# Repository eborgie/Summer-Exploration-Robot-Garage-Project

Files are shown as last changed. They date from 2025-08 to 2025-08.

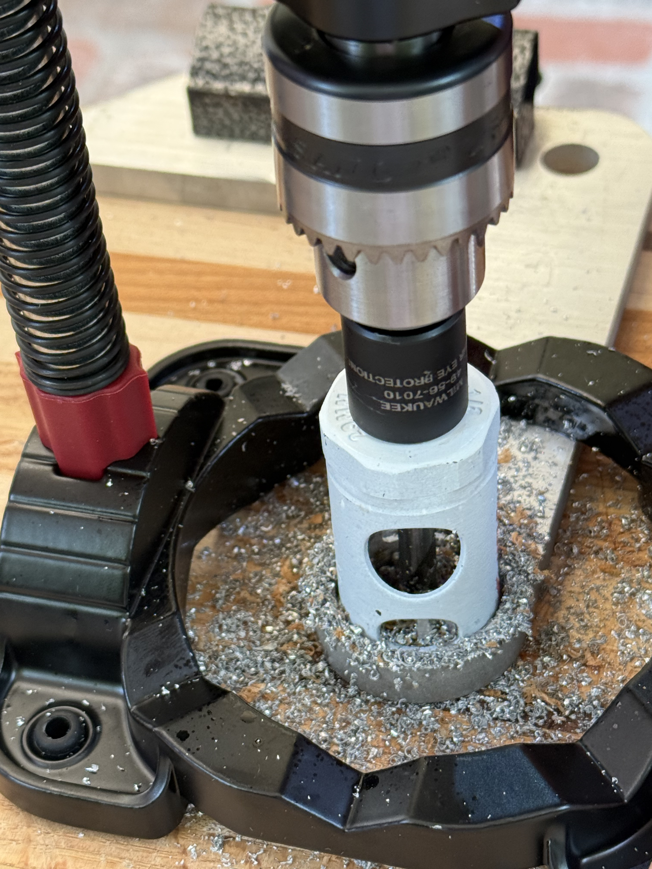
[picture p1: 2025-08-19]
IMG_4325.jpeg

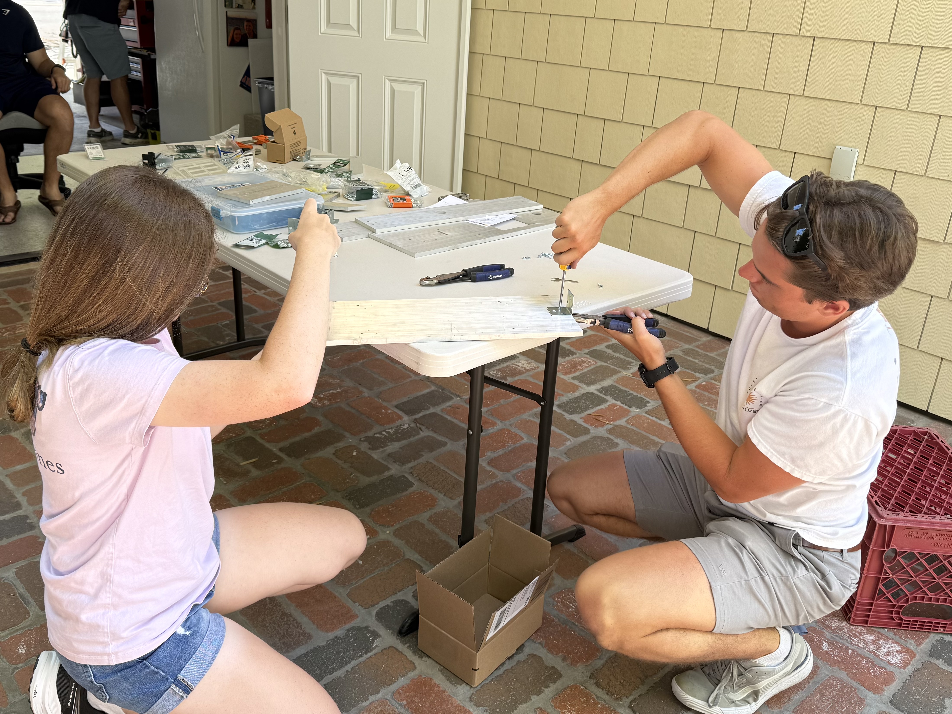
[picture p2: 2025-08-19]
IMG_4257.jpeg

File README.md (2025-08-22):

Iteration 1: Original Aluminum Chassis



Iteration 2: Chassis with Thin Steel sides and Aluminum top and bottom





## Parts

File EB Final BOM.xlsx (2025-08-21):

Final Design BOM | Part Name | # Of Parts | Unit Price | Total Cost | Preliminary sourcing link(s) | Categorical Statistics | Categorical Values
Chassis |  |  |  |  |  | # Of Unique Chassis Parts | 1
Aluminum Sheet |  | 1 | $169.80 | $169.80 | https://www.mcmaster.com/9246k475/ | Total # Of Chassis Parts | 1
 |  |  |  | $0.00 |  | Average Unit Price | $169.80
 |  |  |  | $0.00 |  | Total Chassis Cost | $169.80
 |  |  |  | $0.00 |  | Percent of Current Budget | 15.93%
 |  |  |  | $0.00 |  | Percent of Total Budget | 16.98%
SELECT AND INSERT NEW ROW ABOVE HERE |  |  |  | $0.00
Suspension & Steering |  |  |  |  |  | # Of Unique S&S Parts | 7
Aluminum Sheet |  | 1 | $169.80 | $169.80 | https://www.mcmaster.com/9246k475/ | Total # Of S&S Parts | 13
Wheel tires (4 pack) |  | 2 | $14.97 | $29.94 | https://www.amazon.com/4-Pack-HobbyPark-2-99-inch-Rubber/dp/B071ZX9JB7 | Average Unit Price | $37.37
Series 20 Motor | 195:1 Metal Gearmotor | 6 | $33.07 | $198.42 | https://www.pololu.com/product/3481 | Total S&S Cost | $441.88
dowel pins-short |  | 1 | $9.11 | $9.11 | https://www.mcmaster.com/98381A910/ | Percent of Current Budget | 41.45%
joint bearings |  | 1 | $9.99 | $9.99 | https://www.amazon.com/dp/B0CXXBHWCX?sp_csd=d2lkZ2V0TmFtZT1zcF9kZXRhaWw | Percent of Total Budget | 44.19%
Bolts |  | 1 | $11.15 | $11.15 | https://www.mcmaster.com/91310a124/
female ends |  | 1 | $13.47 | $13.47 | https://www.amazon.com/dp/B0CV43VQHN?aref=0ED2V8mSYO
 |  |  |  | $0.00
 |  |  |  | $0.00
 |  |  |  | $0.00
 |  |  |  | $0.00
SELECT AND INSERT NEW ROW ABOVE HERE |  |  |  | $0.00
Sample Arm |  |  |  |  |  | # Of Unique SA Parts | 4
6mm shaft 2ft [609mm] CHECK ELSEWHERE 6MM | Linear shaft Diameter: 4mm Length: 600mm | 1 | $22.67 | $22.67 | https://shop.pbclinear.com/collections/linear-shafting-and-rails/products/nim04-0600-sl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 | Total # Of SA Parts | 5
Series 20 Motor Extended Shaft | 195:1 Metal Gearmotor with Extended Motor Shaft | 2 | $36.35 | $72.70 | https://www.pololu.com/product/3493 | Average Unit Price | $20.61
Micro Servo | HS-55 Servo-Clockwise (Servo) | 1 | $13.49 | $13.49 | https://www.servocity.com/hs-55-servo/ | Total SA Cost | $118.81
Motor Encoder | Magnetic Encoder Pair Kit for 20D [2 included] | 1 | $9.95 | $9.95 | https://www.pololu.com/product/3499 | Percent of Current Budget | 11.14%
 |  |  |  | $0.00 |  | Percent of Total Budget | 11.88%
SELECT AND INSERT NEW ROW ABOVE HERE |  |  |  | $0.00
Electronics |  |  |  |  |  | # Of Unique Electronics Parts | 9
L298N Motor Controller | 4 Pack L298N Motor Drive Controller Board | 1 | $9.99 | $9.99 | https://www.amazon.com/Controller-H-Bridge-Stepper-Control-Mega2560/dp/B07WS89781?gQT=1 | Total # Of Electronics Parts | 10
Stepper Motor - NEMA 17 |  | 1 | $12.99 | $12.99 | https://www.amazon.com/Stepper-Motor-Bipolar-64oz-Printer/dp/B00PNEQI7W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 | Average Unit Price | $24.88
A4988 Stepper Driver |  | 1 | $10.19 | $10.19 | https://www.amazon.com/HiLetgo-Stepstick-Stepper-Printer-Compatible/dp/B07BND65C8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 | Total Electronics Cost | $250.85
Arduino MEGA |  | 1 | $50.94 | $50.94 | https://www.amazon.com/ARDUINO-MEGA-2560-REV3-A000067/dp/B0046AMGW0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 | Percent of Current Budget | 23.53%
DC-DC Buck Conveter |  | 1 | $11.99 | $11.99 | https://www.amazon.com/XLX-Adjustable-Step-Down-1-25-36V-XL4016E1-Regulating/dp/B07Z8Q6NYX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 | Percent of Total Budget | 25.09%
3S LiPo Battery |  | 1 | $26.99 | $26.99 | https://www.amazon.com/1800mAh-M4-FPV250-Shredder-Nighthawk-Airplane/dp/B013I9SAHO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
XT60 Connector |  | 1 | $13.99 | $13.99 | https://www.amazon.com/dp/B07CN3RZRF?sp_csd=d2lkZ2V0TmFtZT1zcF9kZXRhaWxfdGhlbWF0aWM
Servos | 25 KG Digital Servo [2 included] | 2 | $26.89 | $53.78 | https://www.amazon.com/DS3225-Waterproof-Digital-Aluminium-Steering/dp/B08RJGVH7D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
Rc set |  | 1 | $59.99 | $59.99 | https://www.gobilda.com/element-6-radio-control-system-mode-2/
 |  |  |  | $0.00
 |  |  |  | $0.00
 |  |  |  | $0.00
SELECT AND INSERT NEW ROW ABOVE HERE |  |  |  | $0.00
Interfacing (collars, hubs, couplers, fasteners) |  |  |  |  |  | # Of Unique Interfacing Parts | 5
Shaft Collar | Universal Mounting Hub for 4mm Shaft, M3 Holes [2 included] | 1 | $10.95 | $10.95 | https://www.pololu.com/product/1997 | Total # Of Interfacing Parts | 18
Lazy Susan Bearing | 2" Lazy Susan Turntable | 1 | $3.99 | $3.99 | https://www.amazon.com/Turntable-Bearing-Rotating-Cabinet-Profile/dp/B0BHQQMG71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 | Average Unit Price | $9.19
Dowel Pins | Dowel Pins 1" Diameter, 1.5" Length | 1 | $17.14 | $17.14 | https://www.mcmaster.com/products/dowel-pins/length~10/length~1-1-4/ | Total Interfacing Cost | $84.80
Retaining Rings | Self-Locking External Retaining Rings [50ct] | 1 | $10.86 | $10.86 | https://www.mcmaster.com/90341A103/ | Percent of Total Budget | 8.48%
L Brackets |  | 14 | $2.99 | $41.86 | https://www.mcmaster.com/17715a43/
 |  |  |  | $0.00
SELECT AND INSERT NEW ROW ABOVE HERE |  |  |  | $0.00
Total Budget: | $1000.00
 | Unique Items | Total Part Count | Remaining Budget | Total Cost | Percent of Personal Budget Used:
TOTALS | 11 | 47 | -$66.14 | $1066.14 | 106.61%

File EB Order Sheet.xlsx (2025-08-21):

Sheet: Sheet1
Ordered? | Place |  | Items | Number | Cost | Shipping | Individual Total | Total | Recieved
TRUE | McMaster Carr | Dowel Pins | https://www.mcmaster.com/98381A910/ | 1 | $9.11 | $27.84 | $9.11 | $440.42 | TRUE
TRUE |  | Bolts | https://www.mcmaster.com/91310a124/ | 1 | $11.15 |  | $11.15 |  | TRUE
TRUE |  | Retaining Clips | https://www.mcmaster.com/90341A103/ | 1 | $10.86 |  | $10.86 |  | TRUE
TRUE |  | Brackets | https://www.mcmaster.com/17715a43/ | 14 | $2.99 |  | $41.86 |  | TRUE
TRUE |  | Aluminum | https://www.mcmaster.com/9246k475/ | 2 | $169.80 |  | $339.60 |  | TRUE
TRUE | Amazon | Wheels | https://www.amazon.com/4-Pack-HobbyPark-2-99-inch-Rubber/dp/B071ZX9JB7 | 2 | $14.97 | $0.00 | $29.94 | $248.25 | TRUE
TRUE |  | Bearing | https://www.amazon.com/dp/B0CXXBHWCX?sp_csd=d2lkZ2V0TmFtZT1zcF9kZXRhaWw | 1 | $9.99 |  | $9.99 |  | TRUE
TRUE |  | Rod ends | https://www.amazon.com/dp/B0CV43VQHN?aref=0ED2V8mSYO | 1 | $13.47 |  | $13.47 |  | TRUE
TRUE |  | Motor Drivers | https://www.amazon.com/Controller-H-Bridge-Stepper-Control-Mega2560/dp/B07WS89781?gQT=1 | 1 | $9.99 |  | $9.99 |  | TRUE
TRUE |  | Stepper | https://www.amazon.com/Stepper-Motor-Bipolar-64oz-Printer/dp/B00PNEQI7W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 | 1 | $12.99 |  | $12.99 |  | TRUE
TRUE |  | Stepper Driver | https://www.amazon.com/HiLetgo-Stepstick-Stepper-Printer-Compatible/dp/B07BND65C8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 | 1 | $10.19 |  | $10.19 |  | TRUE
TRUE |  | Arduino | https://www.amazon.com/ARDUINO-MEGA-2560-REV3-A000067/dp/B0046AMGW0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 | 1 | $50.94 |  | $50.94 |  | TRUE
TRUE |  | DCDC buck | https://www.amazon.com/XLX-Adjustable-Step-Down-1-25-36V-XL4016E1-Regulating/dp/B07Z8Q6NYX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 | 1 | $11.99 |  | $11.99 |  | TRUE
TRUE |  | Battery | https://www.amazon.com/1800mAh-M4-FPV250-Shredder-Nighthawk-Airplane/dp/B013I9SAHO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 | 1 | $26.99 |  | $26.99 |  | TRUE
TRUE |  | Nylon wires | https://www.amazon.com/dp/B07CN3RZRF?sp_csd=d2lkZ2V0TmFtZT1zcF9kZXRhaWxfdGhlbWF0aWM | 1 | $13.99 |  | $13.99 |  | TRUE
TRUE |  | servos | https://www.amazon.com/DS3225-Waterproof-Digital-Aluminium-Steering/dp/B08RJGVH7D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 | 2 | $26.89 |  | $53.78 |  | TRUE
TRUE |  | Lazy susan | https://www.amazon.com/Turntable-Bearing-Rotating-Cabinet-Profile/dp/B0BHQQMG71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 | 1 | $3.99 |  | $3.99 |  | TRUE
TRUE | Pololu | Motors | https://www.pololu.com/product/3481 | 6 | $33.07 | $9.17 | $198.42 | $306.59 | TRUE
TRUE |  | Motors with rod | https://www.pololu.com/product/3493 | 2 | $36.35 |  | $72.70 |  | TRUE
TRUE |  | Encoder | https://www.pololu.com/product/3499 | 1 | $9.95 |  | $9.95 |  | TRUE
TRUE |  | Universal adapter | https://www.pololu.com/product/1997 | 1 | $10.95 | $5.40 | $10.95 |  | TRUE
TRUE | Servo City/Gobuilda | Mini servo | https://www.servocity.com/hs-55-servo/ | 1 | $13.45 | $5.12 | $13.45 | $73.40 | TRUE
TRUE |  | Radio controller | https://www.gobilda.com/element-6-radio-control-system-mode-2/ | 1 | $59.95 | $11.99 | $59.95 |  | TRUE
 |  |  |  | 45 |  |  | Total | $1068.66 |  | $534.33 | $581.71
 |  |  |  |  |  |  |  |  |  | $47.38
ROUND 2:
FALSE | Amazon | Dshaft | https://www.amazon.com/Favordrory-Stainless-Straight-Helicopter-Airplane/dp/B08L7X3D13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 | 1 | $7.99 |  | $7.99 |  | FALSE
TRUE | Amazon | Wire | https://www.amazon.com/Silicone-Electrical-electronics-stranded-Flexible/dp/B07TGJGJGD?s=industrial | 1 | $14.58 | $0.00 | $14.58 | $22.57 | TRUE
TRUE | Pololu | Motor | https://www.pololu.com/product/3481 | 1 | $33.07 | $8.66 | $33.07 | $41.73 | TRUE
TRUE | Mcmaster Carr |  | https://www.mcmaster.com/98381A716/ | 1 | $17.14 | $10.20 | $17.14 |  | TRUE
TRUE | mcmaster carr |  | https://www.mcmaster.com/91595A154/ | 4 | $12.48 |  | $3.12 | $30.46 | TRUE
FALSE | servo city | servo | https://www.servocity.com/hs-65hb-servo/ | 1 | $25.49 |  | 25.49 |  | FALSE
FALSE |  |  |  | 9 |  |  | Total | $94.76
FALSE
FALSE
FALSE
FALSE
FALSE
FALSE
FALSE
FALSE
FALSE
FALSE
FALSE
FALSE
FALSE
FALSE
FALSE
FALSE
FALSE
FALSE
FALSE
FALSE
FALSE
FALSE
FALSE
FALSE
FALSE
FALSE
FALSE
FALSE
FALSE
FALSE
FALSE
FALSE
FALSE
FALSE
FALSE
FALSE
FALSE
FALSE
FALSE
FALSE
FALSE
FALSE
FALSE
FALSE
FALSE
FALSE
FALSE
FALSE
FALSE
FALSE
FALSE
FALSE
FALSE
FALSE
FALSE
FALSE
FALSE
FALSE
FALSE
FALSE
FALSE
FALSE
FALSE
FALSE
FALSE
FALSE
FALSE
FALSE
FALSE
FALSE
FALSE
FALSE
FALSE
FALSE
FALSE
FALSE
FALSE
FALSE
FALSE
FALSE
FALSE
FALSE
FALSE
FALSE
FALSE
FALSE
FALSE
FALSE
FALSE
FALSE
FALSE
FALSE
FALSE
FALSE
FALSE
FALSE
FALSE
FALSE
FALSE
FALSE
FALSE
FALSE
FALSE
FALSE
FALSE
FALSE
FALSE
FALSE
FALSE
FALSE
FALSE
FALSE
FALSE
FALSE
FALSE
FALSE
FALSE
FALSE
FALSE
FALSE
FALSE
FALSE
FALSE
FALSE
FALSE
FALSE
FALSE
FALSE
FALSE
FALSE
FALSE
FALSE
FALSE
FALSE
FALSE
FALSE
FALSE
FALSE
FALSE
FALSE
FALSE
FALSE
FALSE
FALSE
FALSE
FALSE
FALSE
FALSE
FALSE
FALSE
FALSE
FALSE
FALSE
FALSE
FALSE
FALSE
FALSE
FALSE
FALSE
FALSE
FALSE
FALSE
FALSE
FALSE
FALSE
FALSE
FALSE
FALSE
FALSE
FALSE
FALSE
FALSE
FALSE
FALSE
FALSE
FALSE
FALSE
FALSE
FALSE
FALSE
FALSE
FALSE
FALSE
FALSE
FALSE
FALSE
FALSE
FALSE
FALSE
FALSE
FALSE
FALSE
FALSE
FALSE
FALSE
FALSE
FALSE
FALSE
FALSE
FALSE
FALSE
FALSE
FALSE
FALSE
FALSE
FALSE
FALSE
FALSE
FALSE
FALSE
FALSE
FALSE
FALSE
FALSE
FALSE
FALSE
FALSE
FALSE
FALSE
FALSE
FALSE
FALSE
FALSE
FALSE
FALSE
FALSE
FALSE
FALSE
FALSE
FALSE
FALSE
FALSE
FALSE
FALSE
FALSE
FALSE
FALSE
FALSE
FALSE
FALSE
FALSE
FALSE
FALSE
FALSE
FALSE
FALSE
FALSE
FALSE
FALSE
FALSE
FALSE
FALSE
FALSE
FALSE
FALSE
FALSE
FALSE
FALSE
FALSE
FALSE
FALSE
FALSE
FALSE
FALSE
FALSE
FALSE
FALSE
FALSE
FALSE
FALSE
FALSE
FALSE
FALSE
FALSE
FALSE
FALSE
FALSE
FALSE
FALSE
FALSE
FALSE
FALSE
FALSE
FALSE
FALSE
FALSE
FALSE
FALSE
FALSE
FALSE
FALSE
FALSE
FALSE
FALSE
FALSE
FALSE
FALSE
FALSE
FALSE
FALSE
FALSE
FALSE
FALSE
FALSE
FALSE
FALSE
FALSE
FALSE
FALSE
FALSE
FALSE
FALSE
FALSE
FALSE
FALSE
FALSE
FALSE
FALSE
FALSE
FALSE
FALSE
FALSE
FALSE
FALSE
FALSE
FALSE
FALSE
FALSE
FALSE
FALSE
FALSE
FALSE
FALSE
FALSE
FALSE
FALSE
FALSE
FALSE
FALSE
FALSE
FALSE
FALSE
FALSE
FALSE
FALSE
FALSE
FALSE
FALSE
FALSE
FALSE
FALSE
FALSE
FALSE
FALSE
FALSE
FALSE
FALSE
FALSE
FALSE
FALSE
FALSE
FALSE
FALSE
FALSE
FALSE
FALSE
FALSE
FALSE
FALSE
FALSE
FALSE
FALSE
FALSE
FALSE
FALSE
FALSE
FALSE
FALSE
FALSE
FALSE
FALSE
FALSE
FALSE
FALSE
FALSE
FALSE
FALSE
FALSE
FALSE
FALSE
FALSE
FALSE
FALSE
FALSE
FALSE
FALSE
FALSE
FALSE
FALSE
FALSE
FALSE
FALSE
FALSE
FALSE
FALSE
FALSE
FALSE
FALSE
FALSE
FALSE
FALSE
FALSE
FALSE
FALSE
FALSE
FALSE
FALSE
FALSE
FALSE
FALSE
FALSE
FALSE
FALSE
FALSE
FALSE
FALSE
FALSE
FALSE
FALSE
FALSE
FALSE
FALSE
FALSE
FALSE
FALSE
FALSE
FALSE
FALSE
FALSE
FALSE
FALSE
FALSE
FALSE
FALSE
FALSE
FALSE
FALSE
FALSE
FALSE
FALSE
FALSE
FALSE
FALSE
FALSE
FALSE
FALSE
FALSE
FALSE
FALSE
FALSE
FALSE
FALSE
FALSE
FALSE
FALSE
FALSE
FALSE
FALSE
FALSE
FALSE
FALSE
FALSE
FALSE
FALSE
FALSE
FALSE
FALSE
FALSE
FALSE
FALSE
FALSE
FALSE
FALSE
FALSE
FALSE
FALSE
FALSE
FALSE
FALSE
FALSE
FALSE
FALSE
FALSE
FALSE
FALSE
FALSE
FALSE
FALSE
FALSE
FALSE
FALSE
FALSE
FALSE
FALSE
FALSE
FALSE
FALSE
FALSE
FALSE
FALSE
FALSE
FALSE
FALSE
FALSE
FALSE
FALSE
FALSE
FALSE
FALSE
FALSE
FALSE
FALSE
FALSE
FALSE
FALSE
FALSE
FALSE
FALSE
FALSE
FALSE
FALSE
FALSE
FALSE
FALSE
FALSE
FALSE
FALSE
FALSE
FALSE
FALSE
FALSE
FALSE
FALSE
FALSE
FALSE
FALSE
FALSE
FALSE
FALSE
FALSE
FALSE
FALSE
FALSE
FALSE
FALSE
FALSE
FALSE
FALSE
FALSE
FALSE
FALSE
FALSE
FALSE
FALSE
FALSE
FALSE
FALSE
FALSE
FALSE
FALSE
FALSE
FALSE
FALSE
FALSE
FALSE
FALSE
FALSE
FALSE
FALSE
FALSE
FALSE
FALSE
FALSE
FALSE
FALSE
FALSE
FALSE
FALSE
FALSE
FALSE
FALSE
FALSE
FALSE
FALSE
FALSE
FALSE
FALSE
FALSE
FALSE
FALSE
FALSE
FALSE
FALSE
FALSE
FALSE
FALSE
FALSE
FALSE
FALSE
FALSE
FALSE
FALSE
FALSE
FALSE
FALSE
FALSE
FALSE
FALSE
FALSE
FALSE
FALSE
FALSE
FALSE
FALSE
FALSE
FALSE
FALSE
FALSE
FALSE
FALSE
FALSE
FALSE
FALSE
FALSE
FALSE
FALSE
FALSE
FALSE
FALSE
FALSE
FALSE
FALSE
FALSE
FALSE
FALSE
FALSE
FALSE
FALSE
FALSE
FALSE
FALSE
FALSE
FALSE
FALSE
FALSE
FALSE
FALSE
FALSE
FALSE
FALSE
FALSE
FALSE
FALSE
FALSE
FALSE
FALSE
FALSE
FALSE
FALSE
FALSE
FALSE
FALSE
FALSE
FALSE
FALSE
FALSE
FALSE
FALSE
FALSE
FALSE
FALSE
FALSE
FALSE
FALSE
FALSE
FALSE
FALSE
FALSE
FALSE
FALSE
FALSE
FALSE
FALSE
FALSE
FALSE
FALSE
FALSE
FALSE
FALSE
FALSE
FALSE
FALSE
FALSE
FALSE
FALSE
FALSE
FALSE
FALSE
FALSE
FALSE
FALSE
FALSE
FALSE
FALSE
FALSE
FALSE
FALSE
FALSE
FALSE
FALSE
FALSE
FALSE
FALSE
FALSE
FALSE
FALSE
FALSE
FALSE
FALSE
FALSE
FALSE
FALSE
FALSE
FALSE
FALSE
FALSE
FALSE
FALSE
FALSE
FALSE
FALSE
FALSE
FALSE
FALSE
FALSE
FALSE
FALSE
FALSE
FALSE
FALSE
FALSE
FALSE
FALSE
FALSE
FALSE
FALSE
FALSE
FALSE
FALSE
FALSE
FALSE
FALSE
FALSE
FALSE
FALSE
FALSE
FALSE
FALSE
FALSE
FALSE
FALSE
FALSE
FALSE
FALSE
FALSE
FALSE
FALSE
FALSE
FALSE
FALSE
FALSE
FALSE
FALSE
FALSE
FALSE
FALSE
FALSE
FALSE
FALSE
FALSE
FALSE
FALSE
FALSE
FALSE
FALSE
FALSE
FALSE
FALSE
FALSE
FALSE
FALSE
FALSE
FALSE
FALSE
FALSE
FALSE
FALSE
FALSE
FALSE
FALSE
FALSE
FALSE
FALSE
FALSE
FALSE
FALSE
FALSE
FALSE
FALSE
FALSE
FALSE
FALSE
FALSE
FALSE
FALSE
FALSE
FALSE
FALSE
FALSE
FALSE
FALSE
FALSE
FALSE
FALSE
FALSE
FALSE
FALSE
FALSE
FALSE
FALSE
FALSE
FALSE
FALSE
FALSE
FALSE
FALSE
FALSE
FALSE
FALSE
FALSE
FALSE
FALSE
FALSE
FALSE
FALSE
FALSE
FALSE
FALSE
FALSE
FALSE
FALSE
FALSE
FALSE
FALSE
FALSE
FALSE
FALSE
FALSE
FALSE
FALSE
FALSE
FALSE
FALSE
FALSE
FALSE
FALSE
FALSE
FALSE
FALSE
FALSE

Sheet: Fasteners
Turntable BOLTS
M3x12 | OR | #5x0.5" | 7x-13x
M3x6 |  | #5x0.25" | 3x
M3 nut [thin] |  |  | 1x
M3x30 |  | #5x1.25" | 1x
M4x35 |  | #8x1.5" | 1x
M4 nut |  |  | 1x
Other Fasteners
M4's
M3's
COST: | $53.45
Paid? | FALSE
THUNDERBIRD PRODUCTS
Cost | $250.00
Tax | $20.63
Total | $270.63
Paid? | FALSE

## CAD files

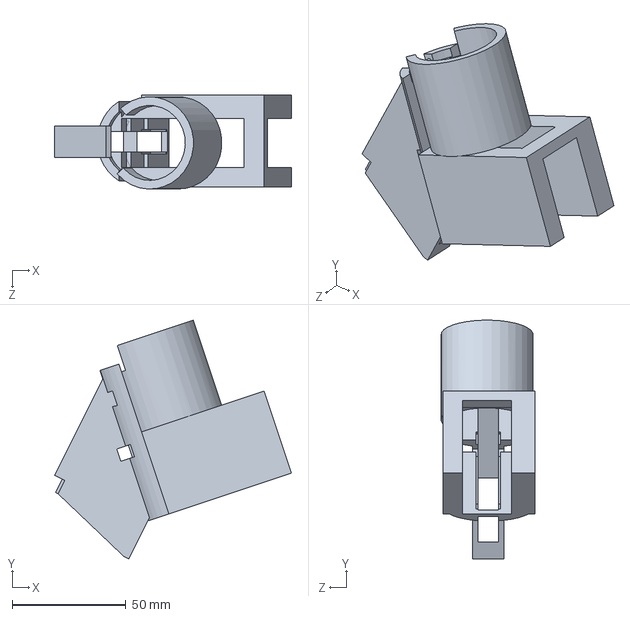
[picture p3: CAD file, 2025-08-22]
RockerPart1redo.SLDPRT
104.4 x 105.1 x 41.4 mm

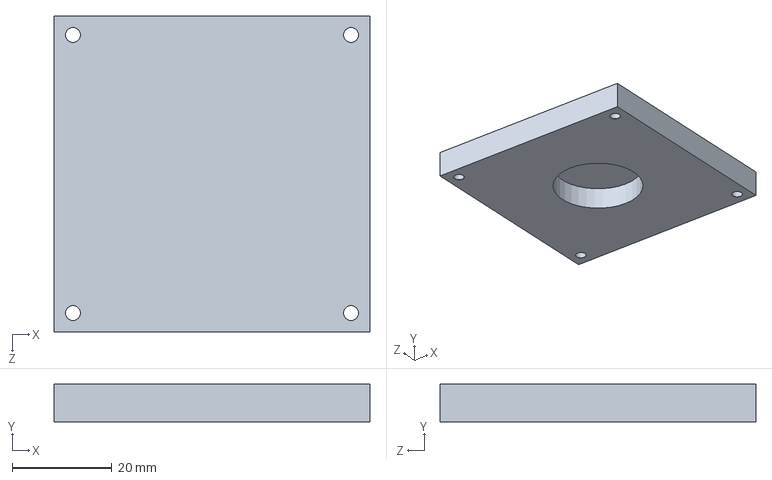
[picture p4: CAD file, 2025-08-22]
BaseHolder.SLDPRT
63.5 x 7.62 x 63.5 mm

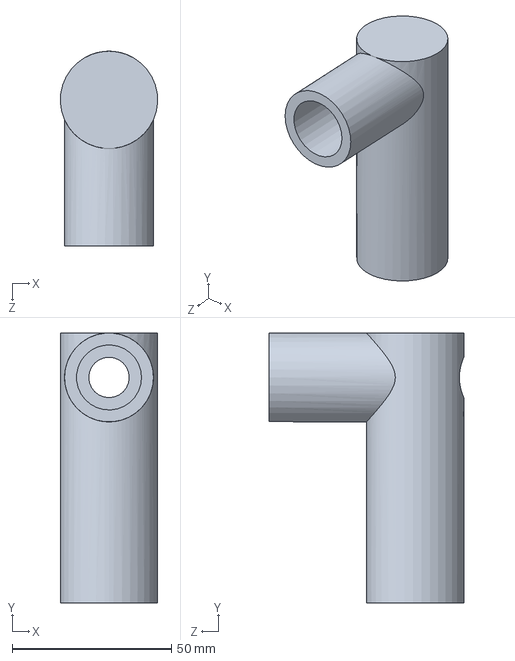
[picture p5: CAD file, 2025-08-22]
spinner (1).SLDPRT
30.6 x 84.9 x 61.2 mm

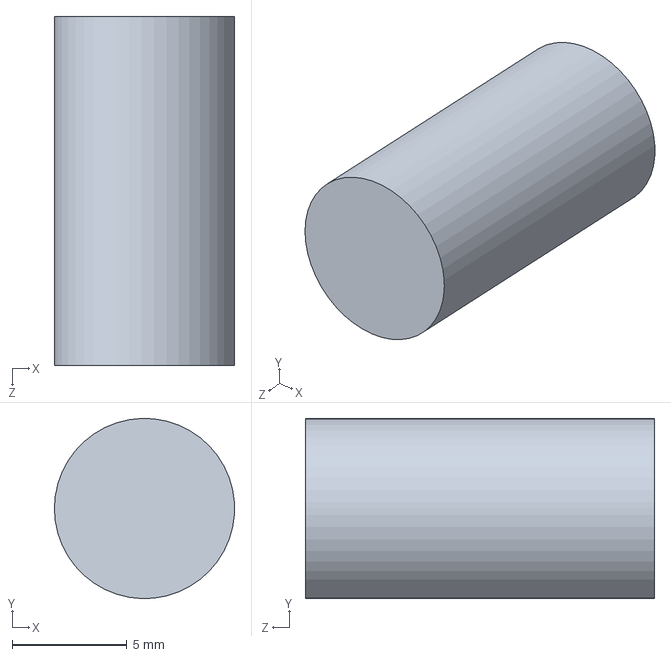
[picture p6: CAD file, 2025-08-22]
bearinghold.SLDPRT
7.85 x 7.85 x 15.2 mm

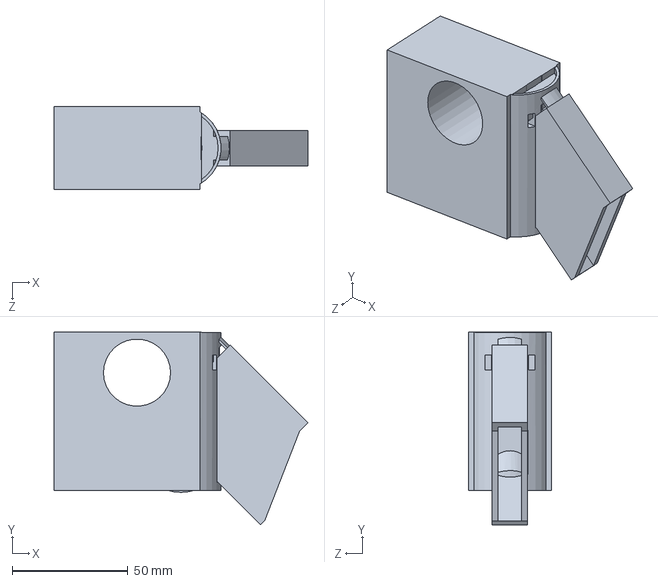
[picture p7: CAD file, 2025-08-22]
BogiePart1.SLDPRT
109.7 x 83.3 x 35.8 mm

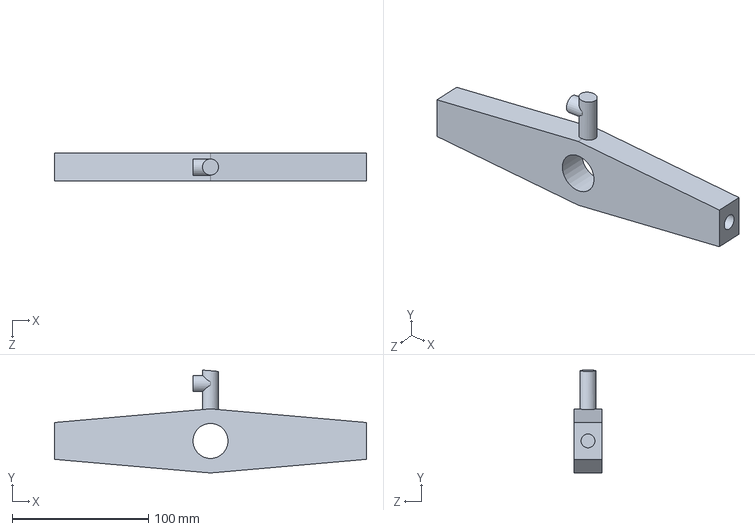
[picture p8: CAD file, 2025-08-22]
Pivot part.1SLDPRT.SLDPRT
228.6 x 75.4 x 20.3 mm

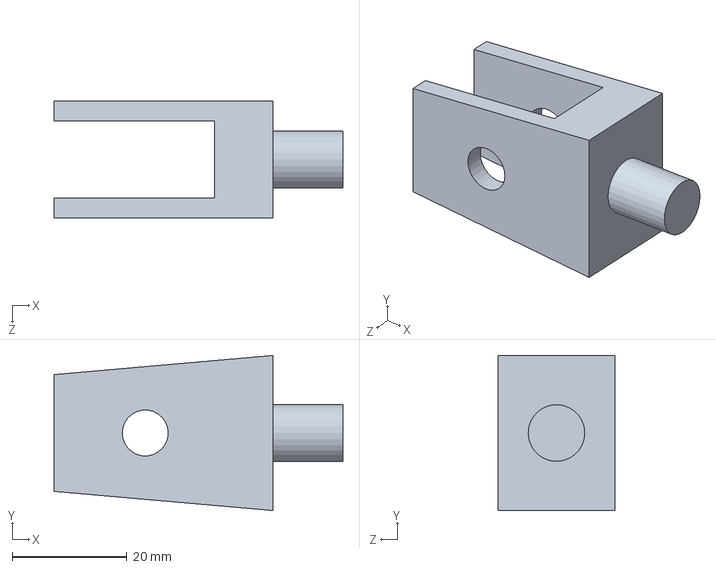
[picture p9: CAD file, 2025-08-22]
Pivot part2.SLDPRT
50.3 x 27.0 x 20.3 mm

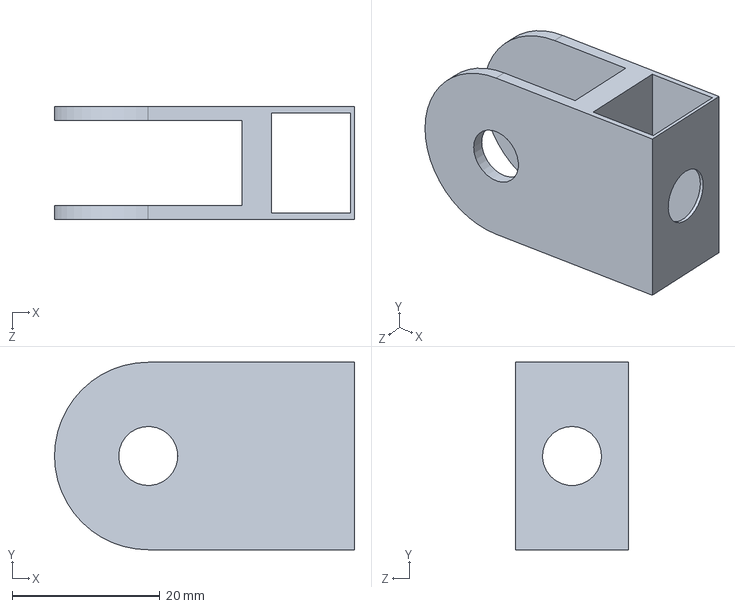
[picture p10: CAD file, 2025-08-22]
ConnectorCover.SLDPRT
40.6 x 25.4 x 15.2 mm

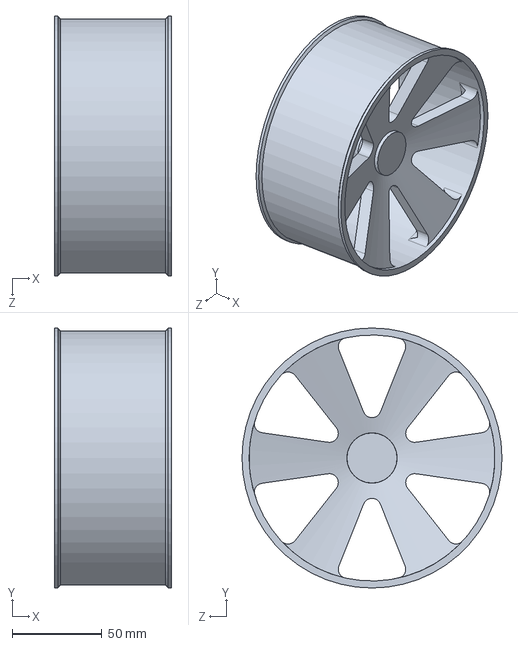
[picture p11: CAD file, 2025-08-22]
BACKWheel.SLDPRT
65.3 x 145.0 x 145.0 mm

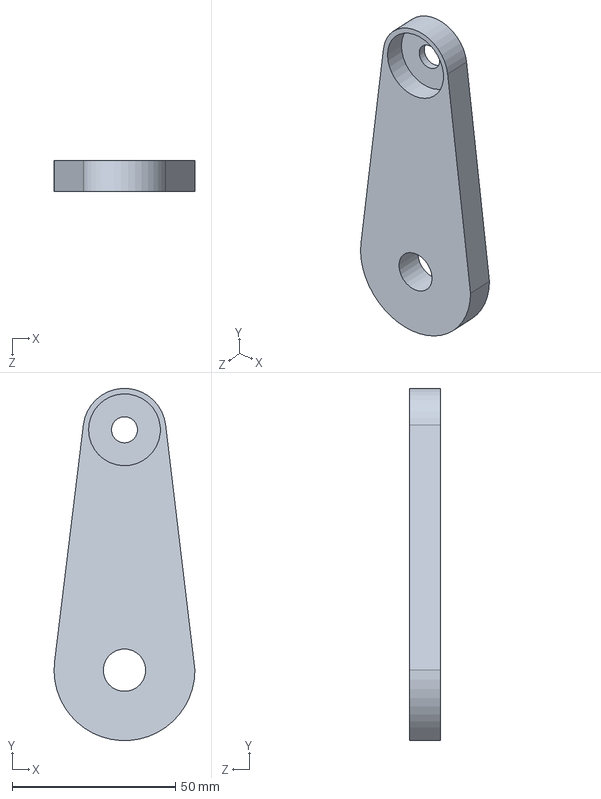
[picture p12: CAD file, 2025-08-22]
linkage.SLDPRT
43.2 x 107.9 x 9.53 mm

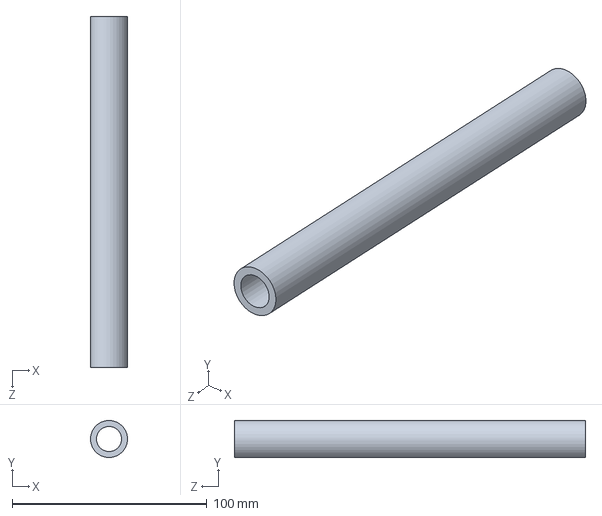
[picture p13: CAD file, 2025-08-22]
dowelpinconnector.SLDPRT
19.1 x 19.0 x 180.3 mm

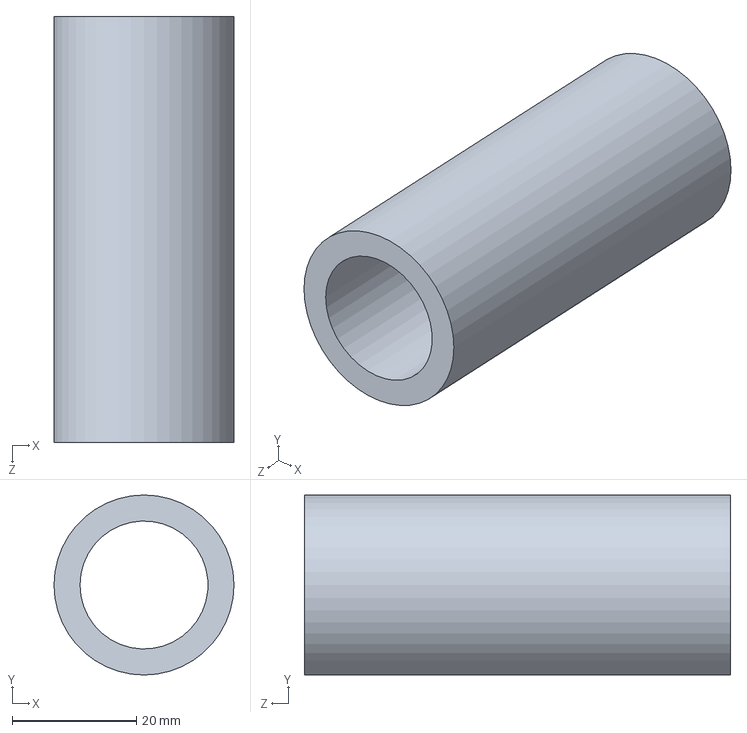
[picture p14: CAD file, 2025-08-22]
middlebogiepart.SLDPRT
29.0 x 29.0 x 68.6 mm

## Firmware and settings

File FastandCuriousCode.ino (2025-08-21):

#include <Servo.h>

#define Ch0_p 2
#define Ch1_p 3
#define Ch2_p 4
#define Ch3_p 5
#define Ch4_p 6
#define Ch5_p 7

// Board 1
#define motorW1_speed 8 // Left front speed
#define motorW1_in1 9 // Left front dir 1
#define motorW1_in2 10 // Left front dir 2
#define motorW2_speed 11 // right front speed
#define motorW2_in3 13  // right front dir1
#define motorW2_in4 12  //right front dir 2

// Board 2
#define motorW3_speed 22 // Left mid speed
#define motorW3_in1 24 // Left mid dir 1
#define motorW3_in2 26 // Left mid dir 2
#define motorW4_speed 27 // right mid speed
#define motorW4_in3 23 // right mid dir 1
#define motorW4_in4 25 // right mid dir 2

// Board 3
#define motorW5_speed 28 // left back speed
#define motorW5_in1 30 // left back dir 1
#define motorW5_in2 32 // left back dir 2
#define motorW6_speed 29 // right back speed
#define motorW6_in3 31 // right back dir 1
#define motorW6_in4 33  // right back dir 2

// servo pins
#define SERVO_FL_PIN 35  // Front Left steering servo
#define SERVO_FR_PIN 37  // Front Right steering servo
#define SERVO_RL_PIN 39  // Rear Left steering servo
#define SERVO_RR_PIN 41  // Rear Right steering servo

Servo servoFL, servoFR, servoBL, servoBR;

// rover geometry constants 
float d1 = 472;  // Distance from center to front/back wheels (mm)
float d2 = 441;  // Distance from center to middle wheels (mm) 
float d3 = 472;  // Distance from center to outer wheels (mm) usually equal to d1
float d4 = 457 ;  // Half of wheelbase (center to left/right wheels) (mm)


int SERVO_CENTER = 180/2;       // Center position 
int SERVO_MAX_ANGLE = 90;     // Max steering angle from center (±90°)
int SERVO_MIN_POS = 0;       // Min servo position 
int SERVO_MAX_POS = 180/2 + 90;      // Max servo position 
float SERVO_SCALE = 1.5;      // scaling factor 

// Calibration variables
int ch0_neutral = 1500;  // Will be auto-calibrated
int ch2_neutral = 1500;  // Will be auto-calibrated
int deadband = 4;
int dcdeadband = 50;       // ±15µs around neutral



float r = 1000;  // Turning radius (mm)
float s = 0;     // Speed percentage (-100% to +100%)

// Speed variables 
float speed1, speed2, speed3;  // Calculated speeds for each wheel position

// Servo angles 
int thetaInnerFront, thetaInnerBack, thetaOuterFront, thetaOuterBack;

void setup() {
  Serial.begin(9600);
  
  // Set receiver pins as inputs
  pinMode(Ch0_p, INPUT);
  pinMode(Ch1_p, INPUT);
  pinMode(Ch2_p, INPUT);
  pinMode(Ch3_p, INPUT);
  pinMode(Ch4_p, INPUT);
  pinMode(Ch5_p, INPUT);
  
 
  // Board 1
  pinMode(motorW1_speed, OUTPUT);
  pinMode(motorW1_in1, OUTPUT);
  pinMode(motorW1_in2, OUTPUT);
  pinMode(motorW2_speed, OUTPUT);
  pinMode(motorW2_in3, OUTPUT);
  pinMode(motorW2_in4, OUTPUT);
  
  // Board 2
  pinMode(motorW3_speed, OUTPUT);
  pinMode(motorW3_in1, OUTPUT);
  pinMode(motorW3_in2, OUTPUT);
  pinMode(motorW4_speed, OUTPUT);
  pinMode(motorW4_in3, OUTPUT);
  pinMode(motorW4_in4, OUTPUT);
  
  // Board 3
  pinMode(motorW5_speed, OUTPUT);
  pinMode(motorW5_in1, OUTPUT);
  pinMode(motorW5_in2, OUTPUT);
  pinMode(motorW6_speed, OUTPUT);
  pinMode(motorW6_in3, OUTPUT);
  pinMode(motorW6_in4, OUTPUT);
  
  // Initialize servos
  servoFL.attach(SERVO_FL_PIN);
  servoFR.attach(SERVO_FR_PIN);
  servoBL.attach(SERVO_RL_PIN);
  servoBR.attach(SERVO_RR_PIN);
  
  
  centerAllServos();
  
  // Stop all motors initially
  stopAllMotors();
  
  Serial.println("=== Complete GoBuilda Rover Control System ===");
  Serial.println("6-Wheel Drive + 4-Wheel Ackermann Steering");
  Serial.println("RC Control with GoBuilda Element-6 System");
  Serial.println("Starting calibration...");
  
  // Auto-calibrate neutral positions
  calibrateChannels();
  
  Serial.println("Calibration complete! Starting rover control...");
  Serial.println("Format: CH0, CH2, Radius(mm), Speed(%), Servo_Angles");
  delay(1000);
}

void loop() {
  // Read PWM signals from GoBuilda Element receiver
  int ch0 = pulseIn(Ch0_p, HIGH, 30000); // Steering
  int ch1 = pulseIn(Ch1_p, HIGH, 30000); 
  int ch2 = pulseIn(Ch2_p, HIGH, 30000); // Throttle
  int ch3 = pulseIn(Ch3_p, HIGH, 30000);
  int ch4 = pulseIn(Ch4_p, HIGH, 30000);
  int ch5 = pulseIn(Ch5_p, HIGH, 30000);
  Serial.print(" ");
  Serial.print(ch0);
  Serial.print(" ");
  Serial.print(ch1);
  Serial.print(" ");
  Serial.print(ch2);
  Serial.print(" ");
  Serial.print(ch3);
  Serial.print(" ");
  Serial.print(ch4);
  Serial.print(" ");
  Serial.print(ch5);
  Serial.print(" ");
  int a= analogRead(SERVO_FL_PIN);
  int b = analogRead(SERVO_FR_PIN);
  Serial.print(" ");
  Serial.print(a);
  Serial.print(" ");
  Serial.print(b);
  Serial.print(" ");
  
  // Only process if we get valid signals
  if (ch0 > 900 && ch0 < 2100 && ch2 > 900 && ch2 < 2100) {
    
    // Convert steering input to turning radius
    if (ch0 > (ch0_neutral + deadband)) {
      // Steering right
      r = map(ch0, ch0_neutral + deadband, 2100, 1500, d4 + 3);
    }
    else if (ch0 < (ch0_neutral - deadband)) {
      // Steering left  
      r = map(ch0, 900, ch0_neutral - deadband, d4 + 2, 1500);
    }
    else {
      // Steering neutral - go straight
      r = 5000; // Very large radius = straight line
    }
    
    // Convert throttle to speed percentage
    if (ch2 > (ch2_neutral + dcdeadband)) {
      // Forward
      s = map(ch2, ch2_neutral + dcdeadband, 2000, 0, 100);
    }
    else if (ch2 < (ch2_neutral - dcdeadband)) {
      // Reverse
      s = map(ch2, ch2_neutral - dcdeadband, 1000, 0, -100);
    }
    else {
      // neutral
      s = 0;
    }
    
    // Control the rover (drive + steering)
    controlRover();
    
    // Print control values for debugging
    Serial.print("CH0: "); Serial.print(ch0);
    Serial.print(", CH2: "); Serial.print(ch2);
    Serial.print(", Radius: "); Serial.print(r);
    Serial.print("mm, Speed: "); Serial.print(s); Serial.print("%");
    Serial.print(", Servos: FL="); Serial.print(thetaInnerFront);
    Serial.print(" FR="); Serial.print(thetaOuterFront);
    Serial.print(" RL="); Serial.print(thetaInnerBack);
    Serial.print(" RR="); Serial.println(thetaOuterBack);
  }
  else {
    // No valid signal received - emergency stop
    Serial.println("No signal - EMERGENCY STOP");
    stopAllMotors();
    centerAllServos();
    s = 0;
    r = 5000;
  }
  
  delay(50); // 20Hz update rate
}

void controlRover() {
  int ch0 = pulseIn(Ch0_p, HIGH, 30000);
  // Calculate motor speeds and servo angles
  calculateMotorsSpeed();
  calculateServoAngles();
  
  // Apply steering angles to servos
  controlSteering();
  
  
  // Apply speeds to motors based on turning direction
  if (abs(ch0 - ch0_neutral) <= deadband) {
    // Going straight - all wheels same speed
    controlLeftMotors(s, s, s);
    controlRightMotors(s, s, s);
  }
  else if (ch0 > (ch0_neutral + deadband)) {
    // Turning RIGHT - left wheels are outer (faster), right wheels are inner (slower)
    controlLeftMotors(speed1, speed2, speed3);   // Left side = outer wheels
    controlRightMotors(speed3, speed2, speed1);  // Right side = inner wheels (reversed order)
  }
  else {
    // Turning LEFT - right wheels are outer (faster), left wheels are inner (slower)  
    controlLeftMotors(speed3, speed2, speed1);   // Left side = inner wheels (reversed order)
    controlRightMotors(speed1, speed2, speed3);  // Right side = outer wheels
  }
}

void calculateMotorsSpeed() {
  // If going straight, all wheels same speed
  if (r > 1000) {
    speed1 = speed2 = speed3 = s;
  }
  else {
    // Outer wheels (furthest from turning point) have maximum speed
    speed1 = s;
    // Inner front and back wheels are closer to turning point
    speed2 = s * sqrt(pow(d3, 2) + pow((r - d1), 2)) / (r + d4);
    // Inner middle wheel is closest to turning point, has lowest speed
    speed3 = s * (r - d4) / (r + d4);
  }
  
  speed1 = constrain(speed1, -100, 100);
  speed2 = constrain(speed2, -100, 100);
  speed3 = constrain(speed3, -100, 100);
}

void calculateServoAngles() {
  // Calculate steering angles for Ackermann geometry
  if (r > 1000) {
    // Going straight - all servos centered
    thetaInnerFront = 0;
    thetaInnerBack = 0;
    thetaOuterFront = 0;
    thetaOuterBack = 0;
  }
  else {
    // Calculate angles based on turning radius
    thetaInnerFront = round((atan((d1 / (r + d4)))) * 180 / PI);
    thetaInnerBack = round((atan((d1 / (r + d4)))) * 180 / PI);
    thetaOuterFront = round((atan((d1 / (r - d4)))) * 180 / PI);
    thetaOuterBack = round((atan((d1 / (r - d4)))) * 180 / PI);
    
    thetaInnerFront = constrain(thetaInnerFront * SERVO_SCALE, -SERVO_MAX_ANGLE, SERVO_MAX_ANGLE);
    thetaInnerBack = constrain(thetaInnerBack * SERVO_SCALE, -SERVO_MAX_ANGLE, SERVO_MAX_ANGLE);
    thetaOuterFront = constrain(thetaOuterFront * SERVO_SCALE, -SERVO_MAX_ANGLE, SERVO_MAX_ANGLE);
    thetaOuterBack = constrain(thetaOuterBack * SERVO_SCALE, -SERVO_MAX_ANGLE, SERVO_MAX_ANGLE);
  }
}

void controlSteering() {
  // Apply steering angles to servos based on turning direction
  int ch0 = pulseIn(Ch0_p, HIGH, 30000);
  if (ch0 > (ch0_neutral + deadband)) {
    // Turning RIGHT
    int leftAngle = constrain(SERVO_CENTER + thetaOuterFront, SERVO_MIN_POS, SERVO_MAX_POS);
    int rightAngle = constrain(SERVO_CENTER - thetaInnerFront, SERVO_MIN_POS, SERVO_MAX_POS);
    
    servoFL.write(leftAngle);    // Left front = outer
    servoFR.write(rightAngle);  // Right front = inner
    servoBL.write(constrain(SERVO_CENTER + thetaOuterBack, SERVO_MIN_POS, SERVO_MAX_POS));
    servoBR.write(constrain(SERVO_CENTER - thetaInnerBack, SERVO_MIN_POS, SERVO_MAX_POS));
    Serial.print(" ");
    Serial.print(leftAngle);
    Serial.print(" ");
    Serial.print(rightAngle);
    Serial.print(" ");
  }
  else if (ch0 < (ch0_neutral - deadband)) {
    // Turning LEFT
    int leftAngle = constrain(SERVO_CENTER - thetaInnerFront, SERVO_MIN_POS, SERVO_MAX_POS);
    int rightAngle = constrain(SERVO_CENTER + thetaOuterFront, SERVO_MIN_POS, SERVO_MAX_POS);
    
    servoFL.write(leftAngle);    // Left front = inner
    servoFR.write(rightAngle);  // Right front = outer
    servoBL.write(constrain(SERVO_CENTER - thetaInnerBack, SERVO_MIN_POS, SERVO_MAX_POS));
    servoBR.write(constrain(SERVO_CENTER + thetaOuterBack, SERVO_MIN_POS, SERVO_MAX_POS));
    Serial.print(" ");
    Serial.print(leftAngle);
    Serial.print(" ");
    Serial.print(rightAngle);
    Serial.print(" ");
  }
  else {
    // Going straight - center all servos
    centerAllServos();
  }
}

void centerAllServos() {
  servoFL.write(SERVO_CENTER);
  servoFR.write(SERVO_CENTER);
  servoBL.write(SERVO_CENTER);
  servoBR.write(SERVO_CENTER);
}

void controlLeftMotors(float frontSpeed, float midSpeed, float backSpeed) {
  // Left Front Motor (Wheel 1) - Driver Board 1, Motor A
  controlSingleMotor(motorW1_speed, motorW1_in1, motorW1_in2, frontSpeed);
  
  // Left Middle Motor (Wheel 2) - Driver Board 1, Motor B
  controlL298NMotorB(motorW2_speed, motorW2_in3, motorW2_in4, midSpeed);
  
  // Left Back Motor (Wheel 3) - Driver Board 2, Motor A
  controlSingleMotor(motorW3_speed, motorW3_in1, motorW3_in2, backSpeed);
}

void controlRightMotors(float frontSpeed, float midSpeed, float backSpeed) {
  // Right Front Motor (Wheel 4) - Driver Board 2, Motor B
  controlL298NMotorB(motorW4_speed, motorW4_in3, motorW4_in4, frontSpeed);
  
  // Right Middle Motor (Wheel 5) - Driver Board 3, Motor A
  controlSingleMotor(motorW5_speed, motorW5_in1, motorW5_in2, midSpeed);
  
  // Right Back Motor (Wheel 6) - Driver Board 3, Motor B
  controlL298NMotorB(motorW6_speed, motorW6_in3, motorW6_in4, backSpeed);
}

void controlSingleMotor(int enablePin, int in1Pin, int in2Pin, float speed) {
  // Convert speed percentage to PWM value (0-255)
  int pwmValue = map(round(abs(speed)), 0, 100, 0, 255);
  pwmValue = constrain(pwmValue, 0, 255);
  
  // Set motor speed
  analogWrite(enablePin, pwmValue);
  
  // Set motor direction
  if (speed > 0) {
    // forward
    digitalWrite(in1Pin, HIGH);
    digitalWrite(in2Pin, LOW);
  }
  else if (speed < 0) {
    // reverse
    digitalWrite(in1Pin, LOW);
    digitalWrite(in2Pin, HIGH);
  }
  else {
    // Stop
    digitalWrite(in1Pin, LOW);
    digitalWrite(in2Pin, LOW);
  }
}

void controlL298NMotorB(int enablePin, int in3Pin, int in4Pin, float speed) {
  // Same as controlSingleMotor but for Motor B (in3/in4) on L298N
  int pwmValue = map(round(abs(speed)), 0, 100, 0, 255);
  pwmValue = constrain(pwmValue, 0, 255);
  
  // Set motor speed
  analogWrite(enablePin, pwmValue);
  
  // Set motor direction
  if (speed > 0) {
    // Forward
    digitalWrite(in3Pin, HIGH);
    digitalWrite(in4Pin, LOW);
  }
  else if (speed < 0) {
    // Reverse
    digitalWrite(in3Pin, LOW);
    digitalWrite(in4Pin, HIGH);
  }
  else {
    // Stop
    digitalWrite(in3Pin, LOW);
    digitalWrite(in4Pin, LOW);
  }
}

void stopAllMotors() {
  // Stop all 6 motors using correct L298N pin assignments
  controlSingleMotor(motorW1_speed, motorW1_in1, motorW1_in2, 0);        // Left Front
  controlL298NMotorB(motorW2_speed, motorW2_in3, motorW2_in4, 0);        // Left Middle  
  controlSingleMotor(motorW3_speed, motorW3_in1, motorW3_in2, 0);        // Left Back
  controlL298NMotorB(motorW4_speed, motorW4_in3, motorW4_in4, 0);        // Right Front
  controlSingleMotor(motorW5_speed, motorW5_in1, motorW5_in2, 0);        // Right Middle
  controlL298NMotorB(motorW6_speed, motorW6_in3, motorW6_in4, 0);        // Right Back
}

void calibrateChannels() {
  Serial.println("Place steering and throttle in NEUTRAL position");
  Serial.println("Calibrating in 3 seconds...");
  delay(3000);
  
  // Calibrate steering channel (CH0)
  Serial.println("Calibrating steering neutral...");
  ch0_neutral = readChannelAverage(Ch0_p, 50);
  Serial.print("CH0 neutral: "); Serial.println(ch0_neutral);
  
  // Calibrate throttle channel (CH2)  
  Serial.println("Calibrating throttle neutral...");
  ch2_neutral = readChannelAverage(Ch2_p, 50);
  Serial.print("CH2 neutral: "); Serial.println(ch2_neutral);
  
  Serial.println();
}

int readChannelAverage(int pin, int samples) {
  long sum = 0;
  int validSamples = 0;
  
  for(int i = 0; i < samples; i++) {
    int value = pulseIn(pin, HIGH, 25000);
    if (value > 900 && value < 2100) { // Valid PWM range
      sum += value;
      validSamples++;
    }
    delay(20);
  }
  
  if (validSamples > 0) {
    return sum / validSamples;
  } else {
    Serial.println("Warning: No valid signals detected");
    return 1500; // Default fallback
  }
}

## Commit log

2025-08-21 Add files via upload
    Project Part Ordering Sheet
    [EB Order Sheet.xlsx]
2025-08-21 Add files via upload
    Original Bill of Materials Sheet
    [EB Final BOM.xlsx]
2025-08-21 Rover Code - Still working on Steering Calibration
2025-08-22 Iteration 1 Order Sheet
    [EB Order Sheet.xlsx]
2025-08-22 Original Bill of Materials
    [EB Final BOM.xlsx]
2025-08-22 3D Printed Parts on Front of Rocker - Steering
    [RockerPart111111.STL, SPINNER_servoSTL.STL]
2025-08-22 3D Printed Part - Middle Bogie
    [middlebogiepart11111.STL]
2025-08-22 SOLIDWORKS CAD Files - 3D Printed
    [BACKWheel.SLDPRT, BaseHolder.SLDPRT, BogiePart1.SLDPRT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]
